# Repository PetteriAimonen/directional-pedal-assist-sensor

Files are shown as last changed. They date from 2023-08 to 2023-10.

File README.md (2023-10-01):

Directional pedal assist sensor
===============================

This repository contains a simple design for pedal assist sensor that does
not require mounting a separate magnet disc to the pedal axle.

Instead, the motion of the chainring is detected using analog hall sensors
and a magnet positioned nearby.

## Goal

Electric assist bicycles use a pedal sensor to control motor activation.
When pedals spin, motor is active - when pedals stop, motor stops.
Actual assist level is controlled separately, by e.g. a handle, torque sensor or accelerometer.

Most common pedal sensor type uses a separate magnet disc, which can be annoying to mount.
The number of magnets on the disc also limit the sensitivity, requiring longer rotation of the cranks before the motor activates.

For bicycles with pedal-activated brakes, it is also important to sense the movement direction.

## Theory of operation

Any ferromagnetic object will distort the magnetic field lines in its vicinity.
Analog [Hall effect](https://en.wikipedia.org/wiki/Hall_effect) sensors are used to detect the passing of the teeth by sensing the variations in the field.

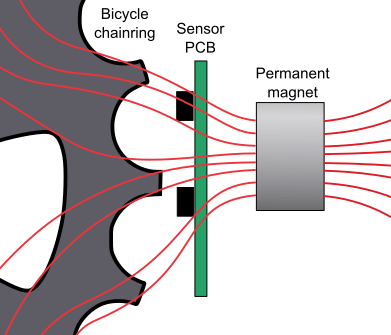
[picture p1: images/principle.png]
Magnetic fields


The measured values are processed to determine middle analog level and then binarized.
After that it can be treated as a [quadrature encoder signal](https://en.wikipedia.org/wiki/Incremental_encoder#Quadrature_outputs).

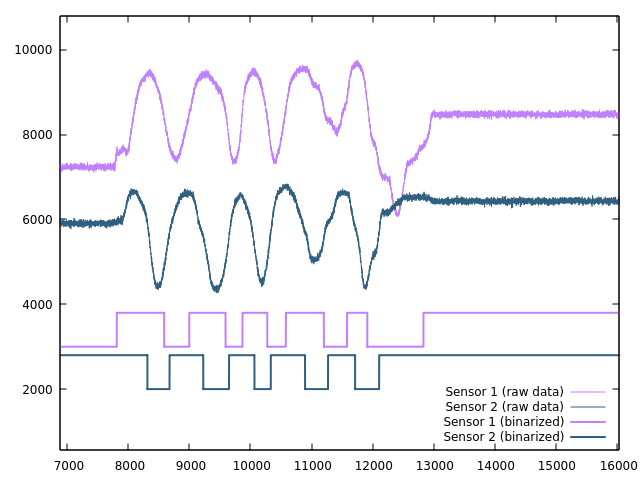
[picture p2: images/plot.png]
Plot of magnetic field levels


This is used to count the number of passing teeth and determine the direction.
After a few teeth in forward direction have passed, signal is sent to motor controller to activate it.
If teeth move in the reverse direction or no pulses are detected within a timeout, the output signal goes back low.

## Circuit and PCB

The circuit is based on ATtiny824 microcontroller and [DRV5053](https://www.ti.com/lit/ds/symlink/drv5053.pdf?ts=1696181784911&ref_url=https%253A%252F%252Fwww.google.com%252F) analog Hall sensors. The built-in ADC is used to read the analog signals.
To improve signal resolution, the DAC is used as a reference voltage and PGA provides 4x gain.

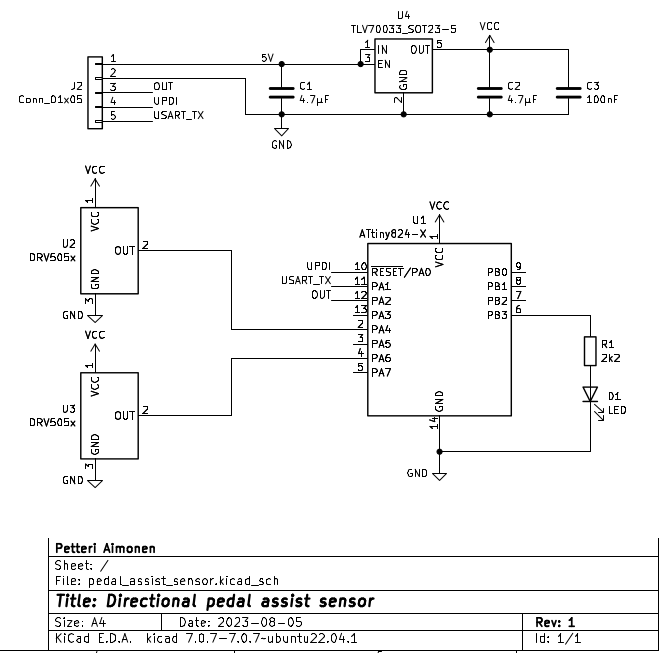
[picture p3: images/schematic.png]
Schematic


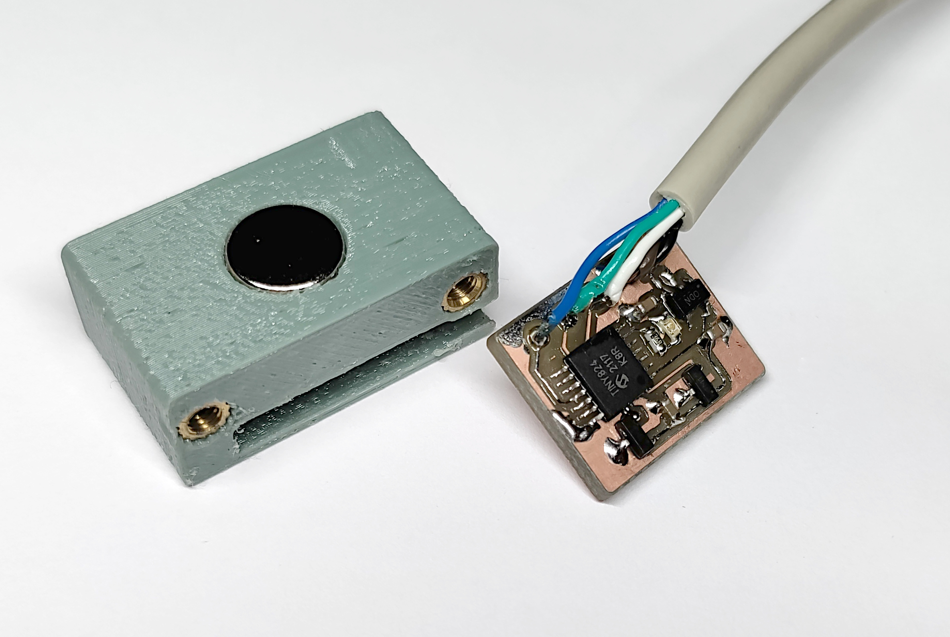
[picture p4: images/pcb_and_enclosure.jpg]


## Software

Software is built using platformio.

To compile, run `pio run`. You can use a USB serial adapter for programming with [pyupdi](https://github.com/mraardvark/pyupdi). Run `pio run -t upload` to program the microcontroller.

There are unit tests that can you can run on PC with `pio test -e native`.

The `main.c` file contains a few settings that can be customized.
By enabling `ENABLE_UART` and `DATA_DUMP` the raw sensor data is written out over 115200 bps UART connection in binary format.
This can then decoded and run through signal processing using `pio run -e native -t exec < testdata.bin`, which will dump out a CSV file.

## Mounting

Positioning is important for reliable operation. For me, it has worked best to have the hall sensors in line with the chainring teeth, and as close as possible.

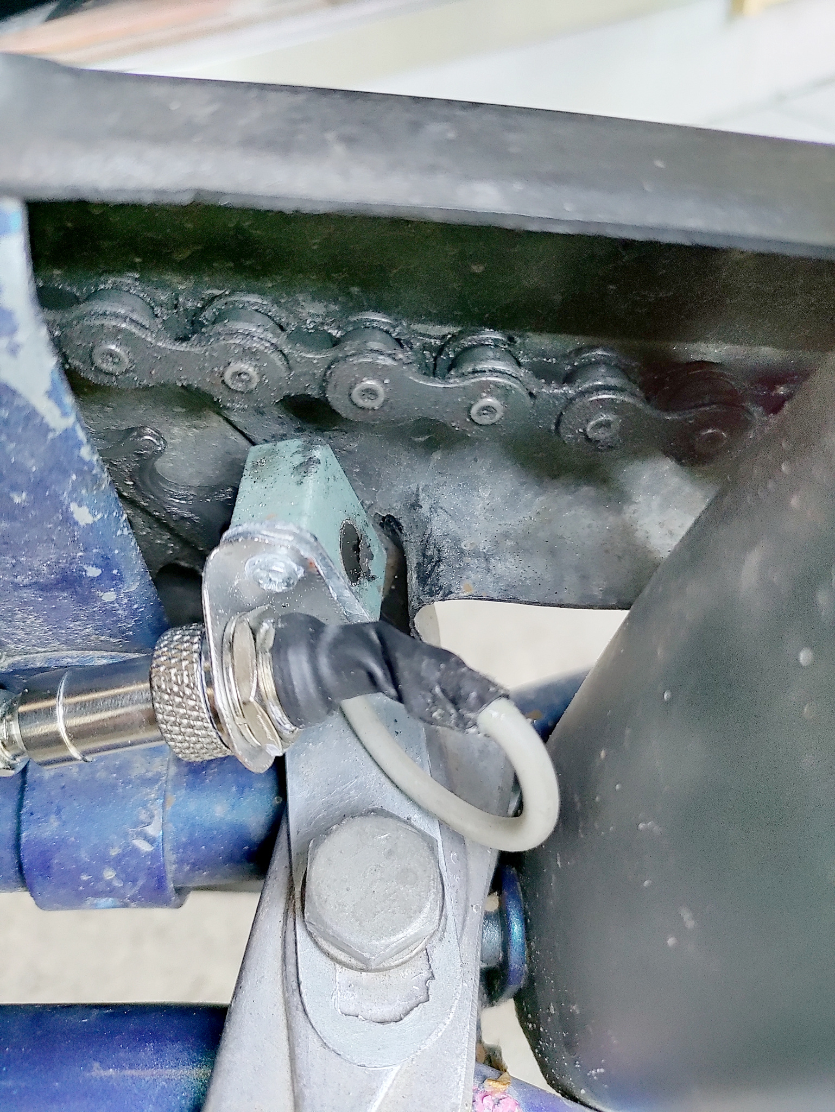
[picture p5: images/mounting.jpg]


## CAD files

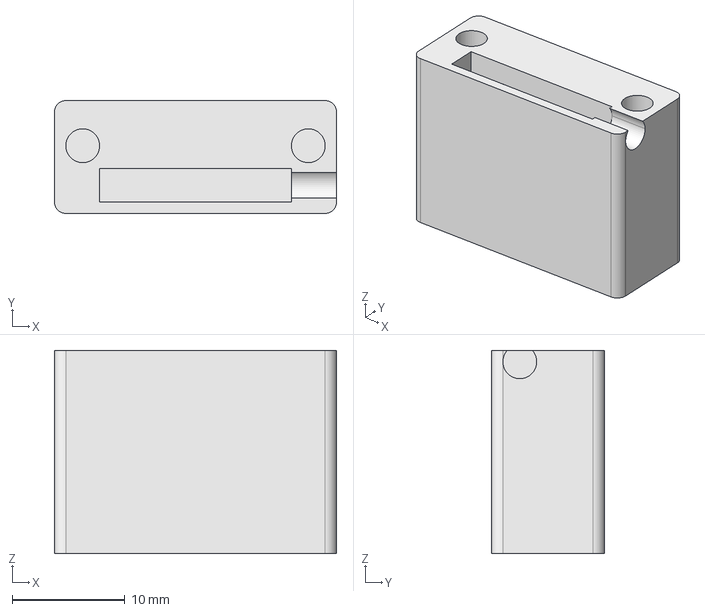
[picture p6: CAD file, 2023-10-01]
enclosure/sensor_enclosure.FCStd
25.0 x 10.0 x 18.0 mm

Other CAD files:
enclosure/sensor_enclosure.stl

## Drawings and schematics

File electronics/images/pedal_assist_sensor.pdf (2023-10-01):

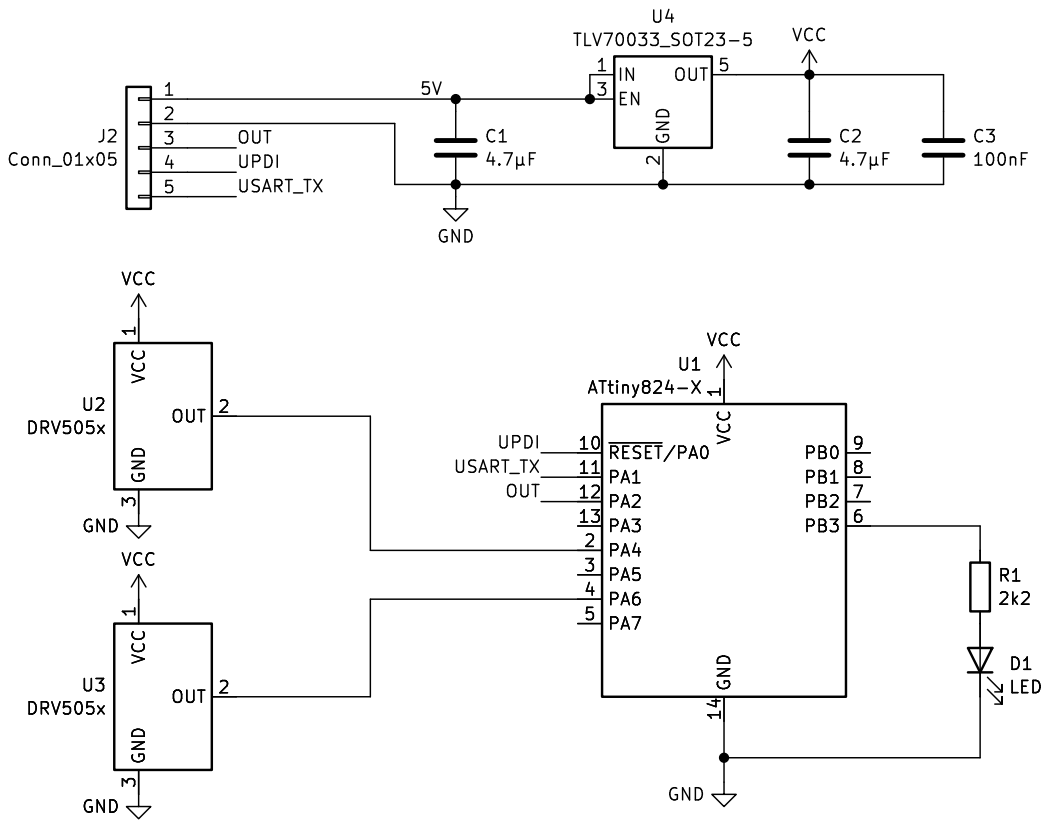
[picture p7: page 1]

Id: 1/1 Title: Directional pedal assist sensor File: pedal_assist_sensor.kicad_sch Sheet: / Petteri Aimonen

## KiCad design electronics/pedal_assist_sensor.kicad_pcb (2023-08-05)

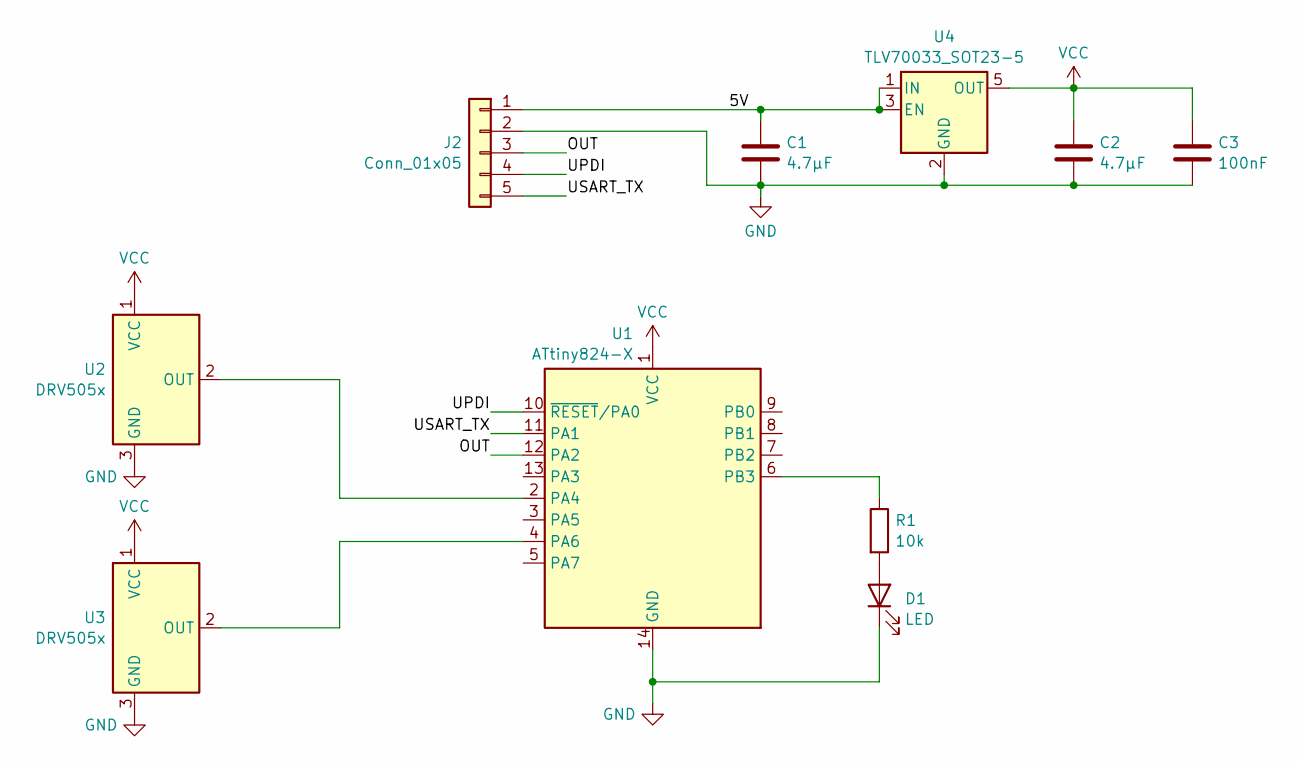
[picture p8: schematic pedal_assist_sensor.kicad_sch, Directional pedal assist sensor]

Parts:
C1, C2: 4.7µF; C_0603_1608Metric
C3: 100nF; C_0603_1608Metric
D1: LED; D_0603_1608Metric
J2: Conn_01x05; PinHeader_1x05_P2.54mm_Vertical
R1: 10k; R_0603_1608Metric
U1: ATtiny824-X; TSSOP-14_4.4x5mm_P0.65mm
U2, U3: DRV505x; SOT-23
U4: TLV70033_SOT23-5; SOT-23-5

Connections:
/5V: C1.1, J2.1, U4.1 (IN), U4.3 (EN)
/OUT: J2.3, U1.12 (PA2)
/UPDI: J2.4, U1.10 (~RESET/PA0)
/USART_TX: J2.5, U1.11 (PA1)
GND: C1.2, C2.2, C3.2, D1.1 (K), J2.2, U1.14 (GND), U2.3 (GND), U3.3 (GND), U4.2 (GND)
unnamed: D1.2 (A), R1.2
unnamed: U1.2 (PA4), U2.2 (OUT)
unnamed: U1.4 (PA6), U3.2 (OUT)
unnamed: R1.1, U1.6 (PB3)
VCC: C2.1, C3.1, U1.1 (VCC), U2.1 (VCC), U3.1 (VCC), U4.5 (OUT)

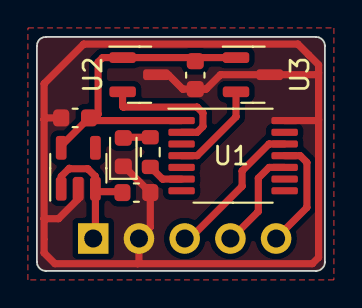
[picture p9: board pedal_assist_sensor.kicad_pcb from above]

Board: 2 copper layers, 16.0 x 13.0 mm, 10 parts (1 on the bottom side), 10 nets.

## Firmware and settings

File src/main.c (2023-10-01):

// This file implements a pedal assist sensor for e-bike use.
// It detects the chainring teeth using linear hall sensors (DRV5053)
// and a magnet.
//
// Pinout:
// PA4 / AIN4: First hall sensor analog signal
// PA6 / AIN6: Second hall sensor analog signal
// PB3:        LED
// PA1:        USART1 TX
// PA2:        Output signal
#define AIN_HALL0   4
#define AIN_HALL1   6
#define LED_PIN     3
#define USART_TX    1
#define OUT_PIN     2

// Detection parameters
// THRESHOLD:  Smaller value gives longer detection distance but is more sensitive to noise
// DECAY:      Smaller value makes min/max follower react faster to DC bias changes
// REVERSE:    Invert fwd/rev directions
// TICKS_FWD:  Minimum number of teeth in forward direction to enable the output
// TICKS_REV:  Minimum number of teeth in backward direction to disable the output
// TIMEOUT:    Time without detection to disable the output (milliseconds)
#define THRESHOLD   512
#define DECAY       10
#define MAXTIME     500
#define MINTIME     10
#define REVERSE     1
#define TICKS_FWD   4
#define TICKS_REV   2
#define TIMEOUT     1000

// IO parameters
// ENABLE_UART: Enable UART output on TX/PA1 pin (if disabled, outputs same as PA2)
// DATA_DUMP:   Instead of gear detection, just dump raw ADC data to UART TX pin
#define ENABLE_UART     0
#define DATA_DUMP       0

#include <avr/io.h>
#include <util/delay.h>
#include "gear_sensor.h"
#include <stdio.h>
#include <stdbool.h>

void setup()
{
    // Set clock to 10 MHz (maximum for 3.3V supply)
    CPU_CCP = CCP_IOREG_gc;
    CLKCTRL.MCLKCTRLB = 0x01;

    // Enable slew rate limitation (reduces noise)
    PORTA.PORTCTRL = PORT_SRL_bm;
    PORTB.PORTCTRL = PORT_SRL_bm;

    // Enable TX and OUT pins
    PORTA.DIR = (1 << USART_TX) | (1 << OUT_PIN);

    // Enable LED output
    PORTB.DIR = (1 << LED_PIN);

#if ENABLE_UART || DATA_DUMP
    // Enable USART1 at 115200 bps
    USART1.BAUD = (64L * F_CPU) / (16 * 115200L);
    USART1.CTRLC = USART_CHSIZE_8BIT_gc;
    USART1.CTRLB = USART_TXEN_bm;
#endif

    // Enable DACREF for subtracting the static magnetic field
    VREF.CTRLA = VREF_AC0REFSEL_2V5_gc;
    VREF.CTRLB = VREF_ADC0REFEN_bm | VREF_AC0REFEN_bm;
    AC0.DACREF = 100;

    // Enable ADC
    // Vref: internal 1.024 V
    // ADCCLK: 2.5 MHz
    // Averaging: 16 samples
    // PGA: enabled, 4x gain
    // PGA negative: DACREF
    ADC0.CTRLA = ADC_ENABLE_bm;
    ADC0.CTRLB = ADC_PRESC_DIV4_gc;
    ADC0.CTRLC = ADC_REFSEL_1024MV_gc | ADC_TIMEBASE2_bm;
    ADC0.CTRLE = 10;
    ADC0.CTRLF = ADC_LEFTADJ_bm | ADC_SAMPNUM_ACC16_gc;
    ADC0.PGACTRL = ADC_GAIN_4X_gc | ADC_PGABIASSEL_1_2X_gc | ADC_ADCPGASAMPDUR_20CLK_gc | ADC_PGAEN_bm;
    ADC0.MUXNEG = ADC_VIA_PGA_gc | ADC_MUXNEG_DACREF0_gc;
    ADC0.COMMAND = ADC_DIFF_bm | ADC_MODE_BURST_SCALING_gc | ADC_START_MUXPOS_WRITE_gc;
}

// Read single ADC channel, with hardware oversampling
int16_t read_adc(int hall_idx)
{
    if (hall_idx == 0)
    {
        ADC0.MUXPOS = ADC_VIA_PGA_gc | AIN_HALL0;
    }
    else
    {
        ADC0.MUXPOS = ADC_VIA_PGA_gc | AIN_HALL1;
    }

    loop_until_bit_is_set(ADC0.INTFLAGS, ADC_RESRDY_bp);
    return (int16_t)ADC0.RESULT;
}

// Adjust PGA negative reference level to keep the signals in measurable range
void adjust_dc_bias(int16_t hall1, int16_t hall2)
{
    static uint8_t dacref = 100;
    if (hall1 > 16384 && hall2 > 16384 && dacref < 255) dacref++;
    if (hall1 < -16384 && hall2 < -16384 && dacref > 0) dacref--;
    AC0.DACREF = dacref;
}

// Continuously send data to serial port
// Format is 5 bytes: SYNC, SENSOR1_LSB, SENSOR1_MSB, SENSOR2_LSB, SENSOR2_MSB.
// Sync byte is always 0xAA. Values encoded as signed 16-bit little-endian.
void dump_data()
{
    uint8_t dacref = 128;

    while(true)
    {
        loop_until_bit_is_set(USART1.STATUS, USART_DREIF_bp);
        USART1.TXDATAL = 0xAA;

        uint16_t hall1 = (uint16_t)read_adc(0);
        loop_until_bit_is_set(USART1.STATUS, USART_DREIF_bp);
        USART1.TXDATAL = (hall1 & 0xFF);
        loop_until_bit_is_set(USART1.STATUS, USART_DREIF_bp);
        USART1.TXDATAL = (hall1 >> 8);

        uint16_t hall2 = (uint16_t)read_adc(1);
        loop_until_bit_is_set(USART1.STATUS, USART_DREIF_bp);
        USART1.TXDATAL = (hall2 & 0xFF);
        loop_until_bit_is_set(USART1.STATUS, USART_DREIF_bp);
        USART1.TXDATAL = (hall2 >> 8);

        adjust_dc_bias(hall1, hall2);
    }
}

int main()
{
    setup();

#if DATA_DUMP
    // Dump raw ADC data over serial port.
    // Use tests/process_dump.c to analyze.
    dump_data();
#endif

    gear_sensor_state_t state = {};
    uint16_t timeout = 0;
    int8_t steps = 0;
    bool output_active = false;

    state.threshold = THRESHOLD;
    state.decay_exp = DECAY;

    while (1)
    {
        // Read ADC values
        int16_t hall1 = read_adc(0);
        int16_t hall2 = read_adc(1);
        adjust_dc_bias(hall1, hall2);

        // Detect gear movement
        int8_t delta = gear_sensor_process(&state, hall1, hall2);

        // Option to reverse direction
        if (REVERSE) delta = -delta;

        // Threshold step count and control output value
        if (delta > 0)
        {
            if (timeout > TIMEOUT)
            {
                // If restarting after timeout, give some
                // time for steps to accumulate.
                timeout = 0;
            }

            // One step forward
            if (steps < TICKS_FWD)
            {
                steps += delta;
            }
            else
            {
                timeout = 0;
                output_active = true;
            }
        }
        else if (delta < 0)
        {
            // One step backward
            if (steps > TICKS_REV)
            {
                steps += delta;
            }
            else
            {
                output_active = false;
            }
        }
        else
        {
            // No steps, keep track of timeout
            if (timeout > TIMEOUT)
            {
                steps = 0;
                output_active = false;
            }
            else
            {
                timeout++;
            }
        }

#if ENABLE_UART
        // Send direction to UART
        if (delta > 0)
        {
            USART1.TXDATAL = 'F';
        }
        else if (delta < 0)
        {
            USART1.TXDATAL = 'R';
        }
#endif

        // Output state on OUT pin and on UART pin (unless UART takes it over)
        if (output_active)
        {
            PORTA.OUTSET = (1 << USART_TX) | (1 << OUT_PIN);
        }
        else
        {
            PORTA.OUTCLR = (1 << USART_TX) | (1 << OUT_PIN);
        }

        // Status indication on LED
        // Blinks for each detected edge, shows the output state
        bool led_state = output_active;
        if (delta != 0)
        {
            led_state = !led_state;
        }

        if (led_state)
            PORTB.OUTSET = (1 << LED_PIN);
        else
            PORTB.OUTCLR = (1 << LED_PIN);
    }
}
